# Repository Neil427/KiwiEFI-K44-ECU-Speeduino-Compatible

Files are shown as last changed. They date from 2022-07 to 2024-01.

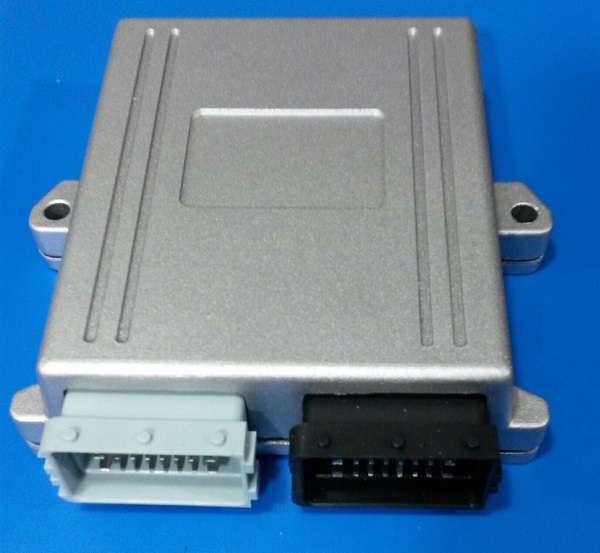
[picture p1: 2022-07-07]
Hardware/KiwiEfi K44 ECU enclosure.png

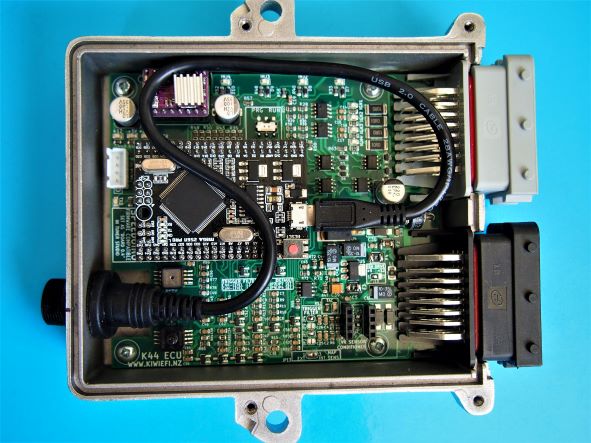
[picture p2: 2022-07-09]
K44_ECU_Inside.JPG

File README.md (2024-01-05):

# Speeduino-KiwiEFI-K44-ECU
The KiwiEFI K44 ECU is designed to run Speeduino firmware and is designed to be 100% compatible with the Speeduino V0.4 Mega2560 pin specification. 
In Tuner Studio select ecu type as V0.4.
  Features:
- 4 layer pcb for good noise immunity, reliable operation.
- 2x 24pin sealed automotive connectors.
- See specifications file for full details.



Open source design for those wishing to build from scratch.

Or will be available for purchase at www.kiwiefi.nz fully built up with mating loom connectors, (firmware/base tune loaded and tested on a real engine) . 

If you would like to save some freight costs and purchase just the pcb fitted with all smd components only (i.e. less box, connectors, arduino, and all other throughhole components) please contact me through www.kiwiefi.nz

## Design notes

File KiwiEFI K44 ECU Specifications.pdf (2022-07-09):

## KiwiEFI K44 Specifications

- 48-pin connector and splash proof case
- 4 injector channels with internal diagnostic LEDs
- 4 Ignition outputs with internal diagnostic LEDs
- CLT, IAT, TPS and O2 inputs
- Inbuilt Hall Effect Sensor blocking diodes and pullups for crank and Cam inputs
- Socket for VR conditioner module(crank and cam input conditioning)
- Inbuilt Baro sensor
- External MAP sensor and internal Map sensor option.
- Socket for DRV8825 stepper module (stepper idle valve control)
- 8 medium-current spare outputs for Fuel pump relay, Fan relay, Boost control, VVT1, VVT2, Idle1, Idle2, Tach + the 4 stepper module outputs.
- Clutch switch digital input.
- Flex fuel digital input.
- 2 spare unassigned digital inputs.
- 2 spare unassigned analog inputs.
- 1 spare unassigned connector pin for custom use.
- Speeduino v0.4 board compatible pin definition, select as board type V0.4 in Tuner Studio
- 2x Serial output, TTL level (Ser0) for Bluetooth on internal connector and RS232 level driver on Secondary Serial (Ser3) TXD and RXD on ecu connector for sending data to dashes etc.
- Uses the same case as the Speeduino Dropbear ECU and is mostly pin compatible with the Dropbear., (the only pinout differences are 1: IG5-IG8 pins are used for digital outputs, as there are only 4 ignition outputs, 2: INJ5-INJ8 pins are fed in parallel with INJ1-INJ4 for paired injectors on a 6/8 cyl, and 3: the CAN bus pins are used for Serial3 RS232 data )

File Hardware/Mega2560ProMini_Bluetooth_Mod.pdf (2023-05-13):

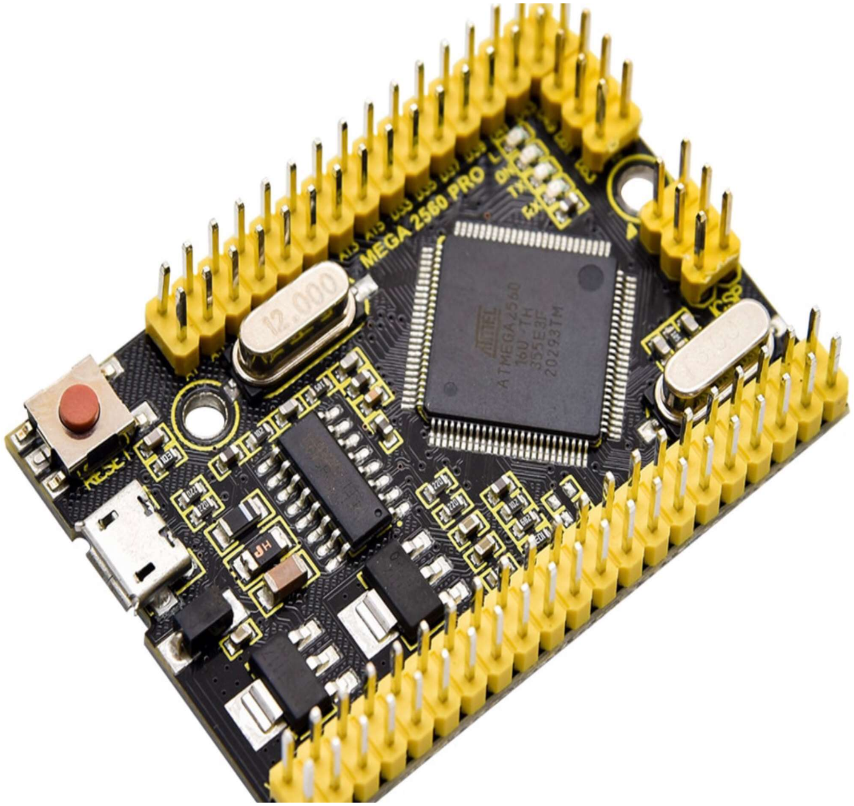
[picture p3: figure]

# MEGA2560 PRO MINI

## Speeduino Serial 0 HC-06 Bluetooth Mod

Note: no guarantee this works with all Pro Mini / HC-06, but works with all I have tried.

The use of blue-tooth connection to Tuner Studio as described in the Speeduino Wiki works on a full sized MEGA2560 board but not on the Pro Mini version. This is due to the value of the resistors used to connect the USB-Serial chip to the TX0/RX0 pins on the MCU chip and header pins.

The full sized Mega2560 that use the 16U2 for USB-Serial conversion have 1K resistors, thus when you attach the blue-tooth module, as in the Speeduino Wiki, it connects to the header pins and thus directly to the MCU pins. The 16U2 chip is still attached to the MEGA TX0/RX0 pins through 1K resistors, the load produced by this can be overcome by the blue-tooth module so it all works.

However the PRO MINI uses a CH340G usb-serial chip connected to the MCU and TX0/RX0 pins through 22R resistors, this low resistance loads the blue-toothTX / Mega RX signal too much stopping the blue-tooth working.

The picture below shows the resistors, one goes to the ProMini TX0 pin and one to the RX0 pin.

The fix I have found to work is to change the 22R (marked as 220 in SMD marking format) that is attached to the ProMini RX0 pin to 220R (either 221 or 2200 in SMD marking format). This reduces the loading on the bluetooth module enough to make it work. You should use a multi-meter to identify which of the two resistors to change as I have found some ProMinis with small layout differences that swap the PCB position of the TX and RX resistors.

(Swapping both resistors does seem to work but it will degrade the low level logic level of the Mega2560 TX0 signal due to the voltage divider produced with the TX LED dropping resistor.)

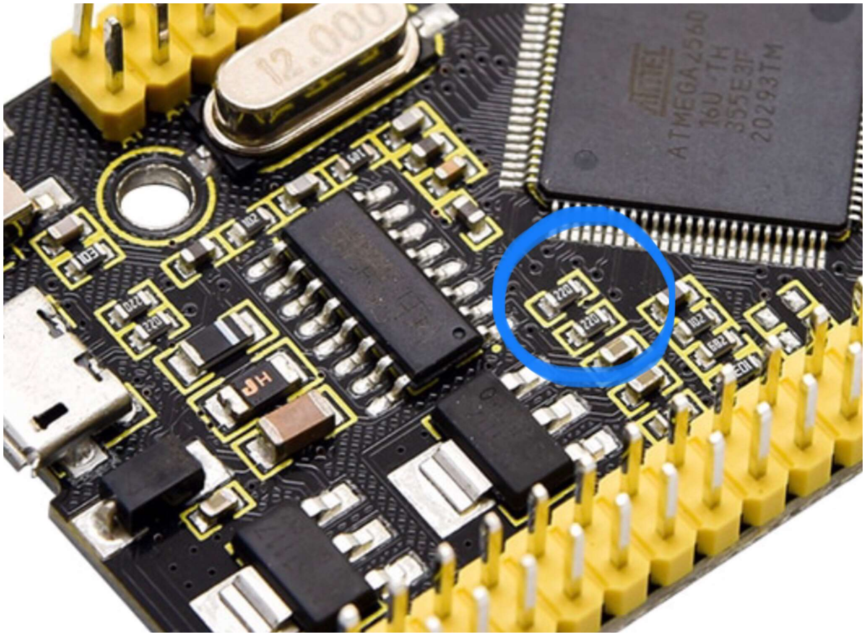
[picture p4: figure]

If you never wish to use Bluetooth you should leave the resistors as 22R as it gives better logic voltage levels between the CH340 and Atmega2560.

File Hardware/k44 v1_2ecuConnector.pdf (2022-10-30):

Sheet1

Page 1

## K44 48-PIN ECU CONNECTOR PINOUT

GREY CONNECTOR | BLACK CONNECTOR
C1 | C2 | C3 | C4 | C5 | C6 | C7 | C8 | C1 | C2 | C3 | C4 | C5 | C6 | C7 | C8
BOOST | FAN | STEP-B2 | STEP-B1 | STEP-A1 | STEP-A2 | FP | GND | GND | AN IN1 | AN IN2 | OXY | CTS | IAT | TPS | MAP
HC4 | LC2 | | | | | LC1 | | SENSOR
B1 | B2 | B3 | B4 | B5 | B6 | B7 | B8 | B1 | B2 | B3 | B4 | B5 | B6 | B7 | B8
IGN1 | IGN2 | IGN3 | IGN4 | IDL2 | IDL1 | VVT1 | VVT2 | TAC | CNK+ | CNK- | CAM+ | CAM- | DIG IN1 | LAUNCH | FLEX
| | | | HC1 | HC3 | HC2 | HC5 | | TRIG1 | TRIG1 | TRIG2 | TRIG2
A1 | A2 | A3 | A4 | A5 | A6 | A7 | A8 | A1 | A2 | A3 | A4 | A5 | A6 | A7 | A8
INJ1 | INJ2 | INJ3 | INJ4 | INJ5 | INJ6 | INJ7 | INJ8 | +12V | GND | +5V OUT | O/P | DIG IN2 | RXD | TXD | GND
| | | | | | | | POWER | POWER | | PIN43 | | SERIAL3 | SERIAL3 | DIGITAL

NOTE: VIEW LOOKING INTO ECU BOX CONNECTORS. (PIN NUMBERS ARE MOLDED INTO REAR OF LOOM CONNECTOR)
A1 | OUTPUT | INJECTOR 1 | A1 | POWER | +12V POWER INPUT From ignition relay
A2 | OUTPUT | INJECTOR 2 | A2 | POWER GROUND | (ground at engine block with its own 1mm wire)
A3 | OUTPUT | INJECTOR 3 | A3 | POWER
A4 | OUTPUT | INJECTOR 4 | A4 | OUTPUT | SPARE OUTPUT DEFAULT SET TO MCU PIN 43
A5 | OUTPUT | INJECTOR 5 | A5 | INPUT | DIGITAL INPUT 2
A6 | OUTPUT | INJECTOR 6 | A6 | COMMS | SERIAL3 DATA RXD
A7 | OUTPUT | INJECTOR 7 | A7 | COMMS | SERIAL3 DATA TXD
A8 | OUTPUT | INJECTOR 8 | A8 | DIGITAL I/P GROUND | GROUND FOR DIGITAL INPUTS AND SERIAL DATA
B1 | OUTPUT | IGNITION 1 | B1 | OUTPUT | TACH OUTPUT Pulled up to +12v
B2 | OUTPUT | IGNITION 2 | B2 | TRIGGER
B3 | OUTPUT | IGNITION 3 | B3 | TRIGGER
B4 | OUTPUT | IGNITION 4 | B4 | TRIGGER
B5 | OUTPUT | IDL2 when configured for 3-wire idle valve | B5 | TRIGGER
B6 | OUTPUT | B6 | INPUT | DIGITAL INPUT 1
B7 | OUTPUT | B7 | INPUT | CLUTCH SWITCH INPUT
B8 | OUTPUT | VVT2 when configured for dual VVT | B8 | INPUT | FLEX FUEL SENSOR INPUT
C1 | OUTPUT | C1 | SENSOR GND
C2 | OUTPUT | C2 | INPUT | ANALOG INPUT 1
C3 | OUTPUT | IDLE STEPPER B2 OUTPUT | C3 | INPUT | ANALOG INPUT 2
C4 | OUTPUT | IDLE STEPPER B1 OUTPUT | C4 | INPUT | OXY SENSOR INPUT 0-5V
C5 | OUTPUT | IDLE STEPPER A1 OUTPUT | C5 | INPUT | COOLANT TEMPERATURE SENSOR
C6 | OUTPUT | IDLE STEPPER A2 OUTPUT | C6 | INPUT | INTAKE AIR TEMPERATURE SENSOR
C7 | OUTPUT | C7 | INPUT | THROTTLE POSITION SENSOR
C8 | POWER GROUND (Ground at engine block with its own 1mm wire) | C8 | INPUT | EXTERNAL MAP SENSOR INPUT (internal Map switch set to EXT.)

+5V SENSOR POWER (MAXCURRENT 100mA)

CRANK SENSOR +ve
CRANK SENSOR -ve (only for VR, for Hall use pin A8) CAM SENSOR +ve
CAM SENSOR -ve (only for VR, for Hall use pin A8) IDL1 SOLENOID gnd active drive VVT1 SOLENOID gnd active drive

BOOST SOLENOID gnd active drive FAN RELAY gnd active drive

FUEL PUMP Gnd active Relay Drive

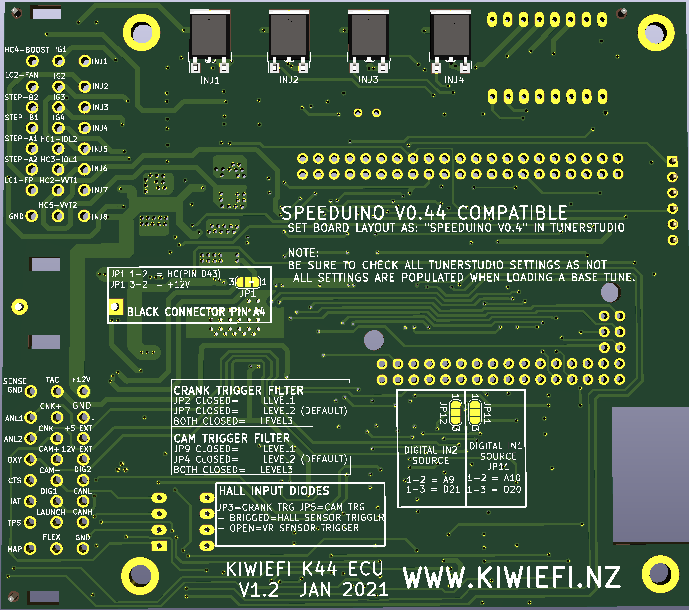
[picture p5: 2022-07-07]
Hardware/PCBbottom.png

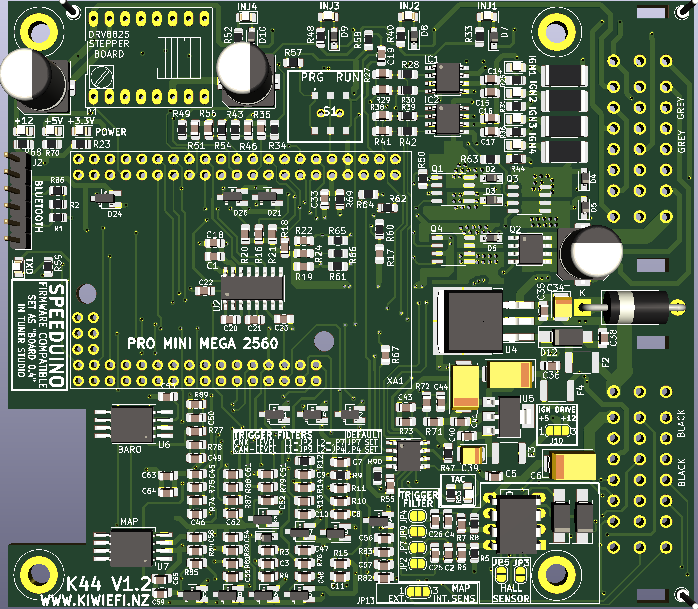
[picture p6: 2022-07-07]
Hardware/PCBtop.png

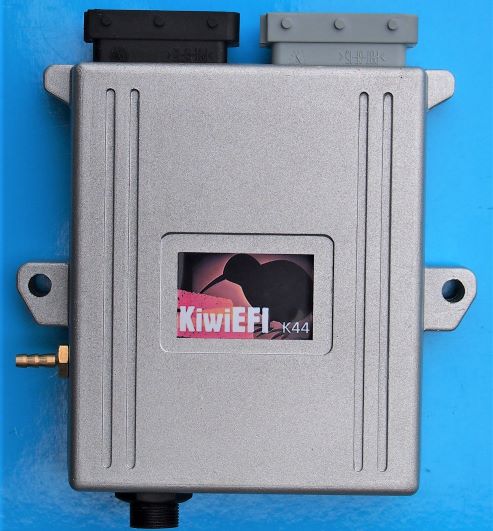
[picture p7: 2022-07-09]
K44_ECU.jpg

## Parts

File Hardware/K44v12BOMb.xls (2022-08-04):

KiwiEFI K44 BOM
Item | Qty | Reference(s) | Value | Footprint
1 | 10 | C1, C15, C17, C20, C21, C22, C23, C33, C63, C65 | 1uF 50V | 0805
2 | 2 | C2, C4 | 10N 50V | 0805
3 | 21 | C3, C5, C7, C9, C14, C16, C18, C35, C36, C38, C40, C41, C43, C45, C47, C51, C53, C54, C58, C61, C64 | 100N 50V | 0805
4 | 3 | C6, C37, C42 | 10uF 25V | Tantalum_Kemet-D
5 | 8 | C8, C10, C11, C44, C48, C52, C55, C59 | 220N 50V | 0805
6 | 2 | C12, C13 | 100uF 35V | Elec_8x10
7 | 1 | C19 | 22uF 50V | 0805
8 | 1 | C24 | 220uF25V | Elec_8x10
9 | 1 | C25 | 4N7 50V | 0805
10 | 1 | C26 | 22N 50V | 0805
11 | 2 | C34, C39 | 47uF 25V | Tantalum_Kemet-B
12 | 4 | C46, C50, C57, C62 | 330N 50V | 0805
13 | 2 | C49, C56 | 47pF 50V | 0805
14 | 1 | D1 | MM3Z5V1ST1G | SOD-323
15 | 9 | D2, D3, D4, D5, D6, D7, D8, D9, D10 | 1N4448WX-TP | SOD-323
16 | 14 | D11, D14, D15, D16, D17, D18, D19, D20, D21, D22, D23, D24, D25, D26 | BAT54S | SOT-23
17 | 1 | D12 | B130-13-F | SMA
18 | 1 | D13 | MR2535L | DO-201AE
19 | 2 | D27, D28 | B130-13-F | SMA
20 | 1 | F2 | 0.5A POLYFUSE | 1812
21 | 2 | F3, F4 | 0.25A POLYFUSE | 1812
22 | 2 | IC1, IC2 | TC4424A | SOIC-8_3.9x4.9mm_P1.27mm
23 | 1 | J1 | Conn_02x24_Male | Delphi_48pinConnectorBox_AandBconnectors
24 | 1 | J2 | BLUETOOTH 1 tx/rx0 | PinHeader_1x06_P2.54mm_Vertical
25 | 3 | J3, J4, J6 | TOOLING HOLE | ToolingHole
26 | 1 | J5 | TRIGGER CONDITIONER | DIP-8_W7.62mm
27 | 12 | LED1, LED2, LED3, LED4, LED5, LED6, LED7, LED8, LED10, LED11, LED12, LED13 | GREEN LED | 0805
28 | 1 | LED9 | BLUE LED | 0805
29 | 1 | P1 | DRV8825 | DRV8825_STEPPER
30 | 3 | Q1, Q3, Q4 | VNS3NV04D | SO-8_3.9x4.9mm_P1.27mm
31 | 2 | Q2, Q7 | NCV8402AD | SOIC-8_3.9x4.9mm_P1.27mm
32 | 4 | Q5, Q6, Q8, Q9 | NCV8408 | ATPAK-2
33 | 3 | R1, R2, R86 | 1K | 0805
34 | 1 | R3 | 1K | 0805
35 | 20 | R4, R11, R14, R16, R17, R18, R19, R20, R21, R22, R24, R27, R29, R35, R38, R41, R46, R51, R55, R56 | 51K | 0805
36 | 13 | R5, R8, R9, R12, R28, R30, R34, R39, R42, R43, R47, R49, R54 | 1K | 0805
37 | 3 | R6, R7, R67 | 220R | 0805
38 | 11 | R10, R13, R72, R74, R76, R77, R79, R81, R82, R85, R87 | 470r | 0805
39 | 1 | R15 | 2K49 | 0805
40 | 1 | R23 | 2K2 | 0805
41 | 9 | R25, R31, R33, R36, R40, R44, R48, R52, R59 | 1K | 0805
42 | 4 | R26, R32, R37, R45 | 10R | 2512
43 | 8 | R50, R60, R61, R62, R63, R64, R65, R66 | 220R | 0805
44 | 2 | R53, R90 | 10K | 0805
45 | 1 | R57 | 10k | 0805
46 | 1 | R58 | 120R | 0805
47 | 1 | R68 | 10K | 0805
48 | 1 | R69 | 10K | 0805
49 | 1 | R70 | 3K9 | 0805
50 | 1 | R71 | 3k9 | 0805
51 | 1 | R73 | 1k | 0805
52 | 4 | R75, R78, R83, R88 | 51k | 0805
53 | 2 | R80, R84 | 2k49 | 0805
54 | 1 | R89 | 1M | 0805
55 | 1 | S1 | SWITCH | AYZ0202AGRLC
56 | 1 | U2 | MAX232 | SOIC-16_3.9x9.9mm_P1.27mm
57 | 1 | U4 | LM2940S-5.0/NOPB | TO-263-3_TabPin2
58 | 1 | U5 | LM2940IMP-5.0/NOPB | SOT-223-3_TabPin2
59 | 1 | U6 | MPXHZ6115A | SSO-8_6.8x5.9mm_P1.27mm
60 | 1 | U7 | MPXHZ6400A | SSO-8_6.8x5.9mm_P1.27mm
61 | 1 | XA1 | Arduino_Mega_Mini | ROBOTDYN Mega2560 PRO MINI 5V (Embed) CH340G

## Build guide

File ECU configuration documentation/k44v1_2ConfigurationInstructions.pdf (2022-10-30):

KiwiEFI K44 ECU CONFIGURATION INSTRUCTIONS V1.2

The K44 is a Speeduino 0.4 compatible ECU using the Mega2560, it uses the Speeduino open source firmware and being 100% compatible with the official hardware version 0.4 it will be able to use all future firmware upgrades written for the 0.4 board.

For documentation and installation instructions for Speeduino ECUs in general please visit wiki.speeduino.com. The following is configuration information specific to the KiwiEFI V44 version of the official Speeduino 0.4 design.
Support and help for Speeduino firmware/hardware can be found at forum.speeduino.com, support and help for the specific KiwiEFI hardware can be obtained via email through our website at KiwiEfi.nz.

## KiwiEFI K44 Specifications

- 48-pin connector and splash proof case
- 4 injector channels with internal diagnostic LEDs
- 4 Ignition outputs with internal diagnostic LEDs
- CLT, IAT, TPS and O2 inputs
- Inbuilt Hall Effect Sensor blocking diodes and pullups for crank and Cam inputs
- Socket for VR conditioner module(crank and cam input conditioning)
- Inbuilt Baro sensor
- External MAP sensor as standard with internal Map sensor available as a optional extra.
- Socket for DRV8825 stepper module (stepper idle valve control)
- 8 medium-current spare outputs for Fuel pump relay, Fan relay, Boost control, VVT1, VVT2, Idle1, Idle2, Tach + the 4 stepper module outputs.
- Clutch switch digital input.
- Flex fuel digital input.
- 2 spare unassigned digital inputs.
- 2 spare unassigned analog inputs.
- Speeduino v0.4 board compatible pin definition, select as board type V0.4 in Tuner Studio
- 2x Serial output, TTL level (Ser0) for Bluetooth on internal connector and RS232 level driver on Secondary Serial (Ser3) TXD and RXD on ecu connector for sending data to dashes etc.
- Uses the same case as the Speeduino Dropbear ECU and is mostly pin compatible with the Dropbear., (the only pinout differences are 1: IG5-IG8 pins are used for digital outputs, as there are only 4 ignition outputs, 2: INJ5-INJ8 pins are fed in parallel with INJ1-INJ4 for paired injectors on a 6/8 cyl, and 3: the CAN bus pins are used for Serial3 RS232 data )

## Board Configuration

The K44 Ecu is compatible with the v0.4 Speeduino configuration, in Tuner Studio setup select board=v0.4.

VR Conditioner – for when using VR crank/cam sensors

Depending on the type of crank and cam sensors you have, there are jumpers that may need to be set. The factory configuration is for Hall effect sensors and Medium signal filtering.

Some VR sensors can send very high AC voltage into the ECU. If you are unsure of your sensor type identify it before connecting it. Using a VR sensor without a VR conditioner may cause damage to the board.

# Jumper Configuration

S1 – PROG-RUN SWITCH
– PROG set to this to update firmware
- RUN set to this for normal operation (default)

J2 – BLUETOOTH CONNECTOR
The Bluetooth connector provides a connection point for a HC-05 Bluetooth module, it is strongly recommended to mount the module or at least its antenna outside the ECU case as the metal case will seriously impact on the range and reliability of the connection.

PIN
1 – HC-05 module (not used) | – connects to MCU D3
2 – HC-05 module pin2 | – connects to VCC
3 – HC-05 module pin3 | – connects to GND
4 – HC-05 module pin4 TXD | – connects to MCU D0 RXD
5 – HC-05 module pin5 RXD | -- connects to MCU D1 TXD
6 – HC-05 module (not used) | -- No Connection

See Speeduino Wiki for Bluetooth configuration details.

Note: the Arduino Mega2560 Pro mini used in this ECU requires 2 resistors to be changed in order to use the Bluetooth option. If your K44 Ecu is purchased as a completed unit from the KiwiEfi.NZ website this modification will have already been done. For details of this modification please contact KiwiEFI.

# Jumpers on Top side of circuit board

Solder jumpers on the top side of the circuit board configure options that may be required to configure the ECU to a specific engine.

JP10 – IGN DRIVE – connect | 1-2 = 5V drive voltage (default) 2-3 = 12V drive voltage
JP13 – MAP SENSOR – connect | 1-2 = External sensor (default) 2-3 = Internal sensor if fitted

We recommend using an external sensor, a wired sensor with short hose to the manifold is faster acting than a long hose to the ECU. An internal sensor of 1bar, 2.5bar, or 4bar is a option available at time of order, or can be fitted later if required.

JP3 & JP5 – HALL SENSOR SELECT
- JOINED = Crank and Cam sensors are Hall effect sensors (default)
- OPEN = Crank and Cam sensors are conditioned by a VR conditioner module NOTE: Make sure these jumpers are OPEN before installing a VR Conditioner module.

CRANK SENSOR FILTER
JP2 joined – TRIGGER FILTER – Crank sensor Level 1 filter
JP7 joined – TRIGGER FILTER – Crank sensor Level 2 filter (default) BOTH JP2 & JP7 joined – Crank sensor Level 3 filter

CAM SENSOR FILTER
JP9 joined – TRIGGER FILTER – Cam sensor Level 1 filter
JP4 joined – TRIGGER FILTER – Cam sensor Level 2 filter (default) BOTH JP9 & JP4 joined – Cam sensor Level 3 filter

## Jumpers on Underside of circuit board

## FACTORY SET - Usually Wont Ever Need To Be Changed

JP11 – DIGIN1 - | 1-2 = connected to function controlled by Arduino pin A10 2-3 = connected to function controlled by Arduino pin D20 (default) (VSS)
JP12 – DIGIN2 - | 1-2 = connected to function controlled by Arduino pin A9 2-3 = connected to function controlled by Arduino pin D21 (default)

JP1 – BLACK ECU PLUG pin A4 – 1-2 = connected to HC o/p controlled by Arduino pin D43
| 2-3 = connected to +12V (for sensors requiring 12V pwr) (default is Connected to D43)

K44 48-PIN ECU CONNECTOR PINOUT

GREY CONNECTOR | BLACK CONNECTOR
C1 | C2 | C3 | C4 | C5 | C6 | C7 | C8 | C1 | C2 | C3 | C4 | C5 | C6 | C7 | C8
BOOST | FAN | STEP-B2 | STEP-B1 | STEP-A1 | STEP-A2 | FP | GND | GND | AN IN1 | AN IN2 | OXY | CTS | IAT | TPS | MAP
HC4 | LC2 | | | | | LC1 | | SENSOR
B1 | B2 | B3 | B4 | B5 | B6 | B7 | B8 | B1 | B2 | B3 | B4 | B5 | B6 | B7 | B8
IGN1 | IGN2 | IGN3 | IGN4 | IDL2 | IDL1 | VVT1 | VVT2 | TAC | CNK+ | CNK- | CAM+ | CAM- | DIG IN1 | LAUNCH | FLEX
| | | | HC1 | HC3 | HC2 | HC5 | | TRIG1 | TRIG1 | TRIG2 | TRIG2
A1 | A2 | A3 | A4 | A5 | A6 | A7 | A8 | A1 | A2 | A3 | A4 | A5 | A6 | A7 | A8
INJ1 | INJ2 | INJ3 | INJ4 | INJ5 | INJ6 | INJ7 | INJ8 | +12V | GND | +5V OUT | O/P | DIG IN2 | RXD | TXD | GND
| | | | | | | | POWER | POWER | | PIN43 | | SERIAL3 | SERIAL3 | DIGITAL

NOTE: VIEW LOOKING INTO ECU BOX CONNECTORS. (PIN NUMBERS ARE MOLDED INTO REAR OF LOOM CONNECTOR)
A1 | OUTPUT | INJECTOR 1 | A1 | POWER | +12V POWER INPUT From ignition relay
A2 | OUTPUT | INJECTOR 2 | A2 | POWER GROUND | (ground at engine block with its own 1mm wire)
A3 | OUTPUT | INJECTOR 3 | A3 | POWER
A4 | OUTPUT | INJECTOR 4 | A4 | OUTPUT | SPARE OUTPUT DEFAULT SET TO MCU PIN 43
A5 | OUTPUT | INJECTOR 5 | A5 | INPUT | DIGITAL INPUT 2
A6 | OUTPUT | INJECTOR 6 | A6 | COMMS | SERIAL3 DATA RXD
A7 | OUTPUT | INJECTOR 7 | A7 | COMMS | SERIAL3 DATA TXD
A8 | OUTPUT | INJECTOR 8 | A8 | DIGITAL I/P GROUND | GROUND FOR DIGITAL INPUTS AND SERIAL DATA
B1 | OUTPUT | IGNITION 1 | B1 | OUTPUT | TACH OUTPUT Pulled up to +12v
B2 | OUTPUT | IGNITION 2 | B2 | TRIGGER | CRANK SENSOR +ve
B3 | OUTPUT | IGNITION 3 | B3 | TRIGGER | CRANK SENSOR -ve (only for VR, for Hall use pin A8)
B4 | OUTPUT | IGNITION 4 | B4 | TRIGGER | CAM SENSOR +ve
B5 | OUTPUT | IDL2 when configured for 3-wire idle valve | B5 | TRIGGER | CAM SENSOR -ve (only for VR, for Hall use pin A8)
B6 | OUTPUT | IDL1 SOLENOID gnd active drive | B6 | INPUT | DIGITAL INPUT 1
B7 | OUTPUT | VVT1 SOLENOID gnd active drive | B7 | INPUT | CLUTCH SWITCH INPUT
B8 | OUTPUT | VVT2 when configured for dual VVT | B8 | INPUT | FLEX FUEL SENSOR INPUT
C1 | OUTPUT | BOOST SOLENOID gnd active drive | C1 | SENSOR GND
C2 | OUTPUT | FAN RELAY gnd active drive | C2 | INPUT | ANALOG INPUT 1
C3 | OUTPUT | IDLE STEPPER B2 OUTPUT | C3 | INPUT | ANALOG INPUT 2
C4 | OUTPUT | IDLE STEPPER B1 OUTPUT | C4 | INPUT | OXY SENSOR INPUT 0-5V
C5 | OUTPUT | IDLE STEPPER A1 OUTPUT | C5 | INPUT | COOLANT TEMPERATURE SENSOR
C6 | OUTPUT | IDLE STEPPER A2 OUTPUT | C6 | INPUT | INTAKE AIR TEMPERATURE SENSOR
C7 | OUTPUT | FUEL PUMP Gnd active Relay Drive | C7 | INPUT | THROTTLE POSITION SENSOR
C8 | POWER GROUND (Ground at engine block with its own 1mm wire) | C8 | INPUT | EXTERNAL MAP SENSOR INPUT (internal Map switch set to EXT.)

+5V SENSOR POWER (MAXCURRENT 100mA)

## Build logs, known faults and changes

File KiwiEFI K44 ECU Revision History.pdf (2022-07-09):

KiwiEFI_K44 Version History

V1.0 - Beta1 pcb design to verify schematic and pcb, minor issues found with mounting holes and connector hole positions. Tested on LS1 V8 with no problems.

V1.01 - Beta 2 pcb test version to confirm mechanical changes to the pcb, cutout for USB cable connector added.

V1.1 - First fully built up ecu tested for 12 months on daily driven LS1 V8 with no failures.
- error found with flyback diode connection for digital outputs, corrected with link on back of pcb.

V1.2 – Work on tidying up a few things before first release.
– PCB change to correct the error with flyback diode connection found in V1.1 pcb.
– Heatsink area on digital output drivers increased to align closer to datasheet recomendations.
– Remove the underside jumpers to select the IGN5-8 alternative function for the IDL,IDL2,VVT,VVT2 connector pins. (Originally these jumpers were to make the ecu 100% pinout compatible with the Dropbear ecu that I was Beta testing on the same vehicle).

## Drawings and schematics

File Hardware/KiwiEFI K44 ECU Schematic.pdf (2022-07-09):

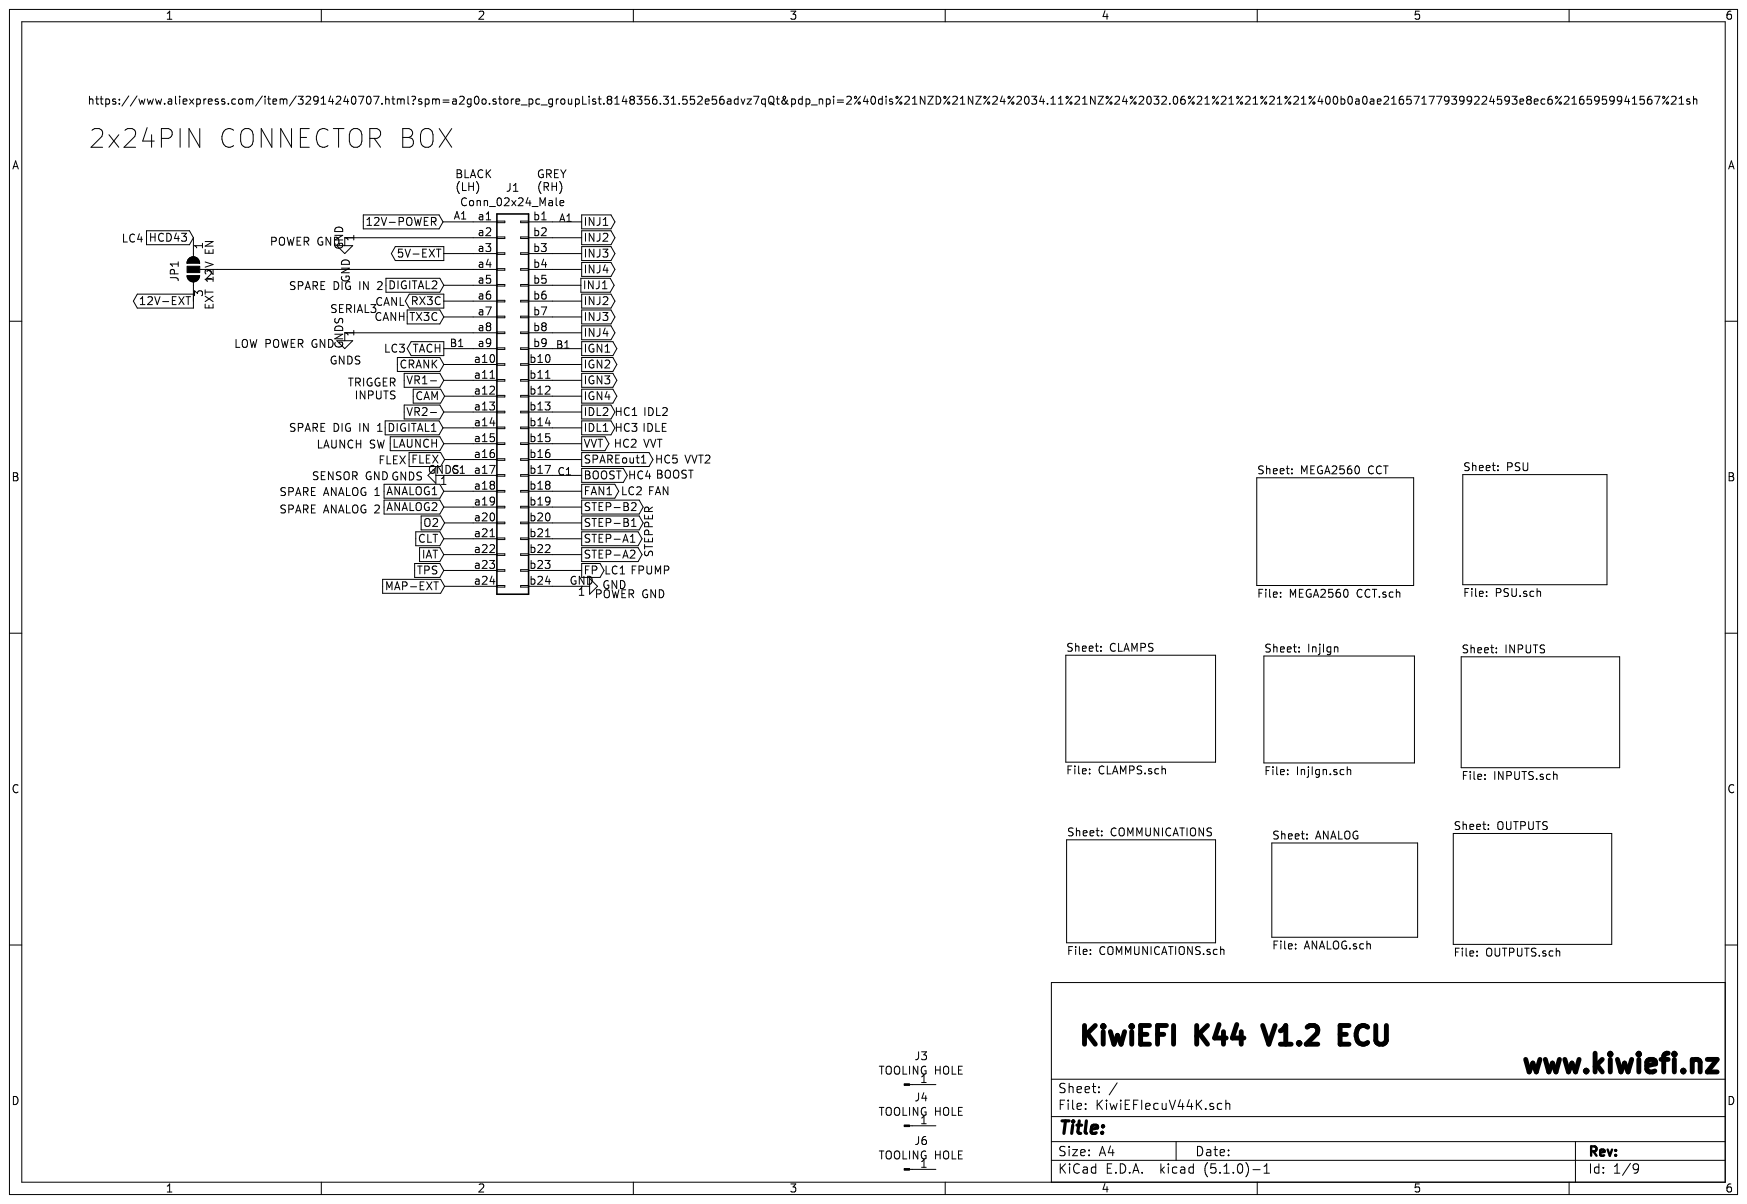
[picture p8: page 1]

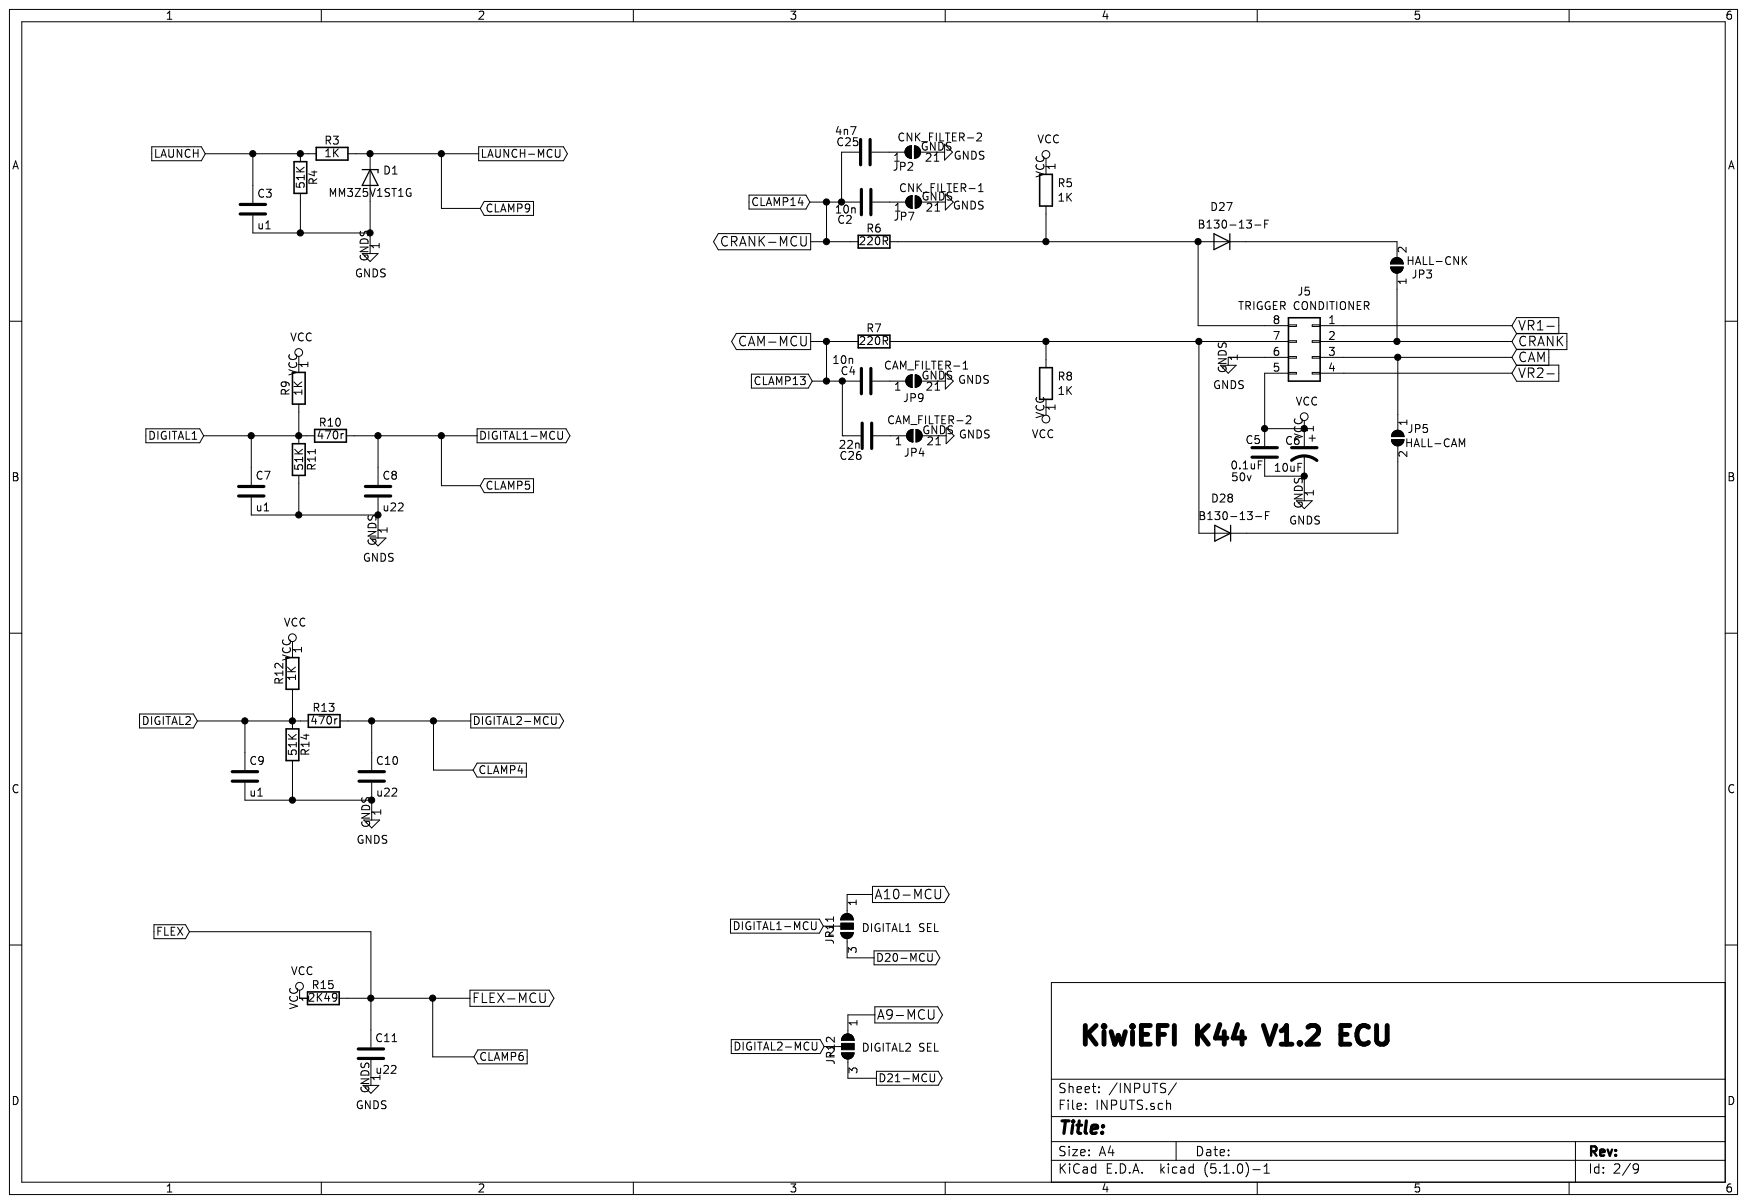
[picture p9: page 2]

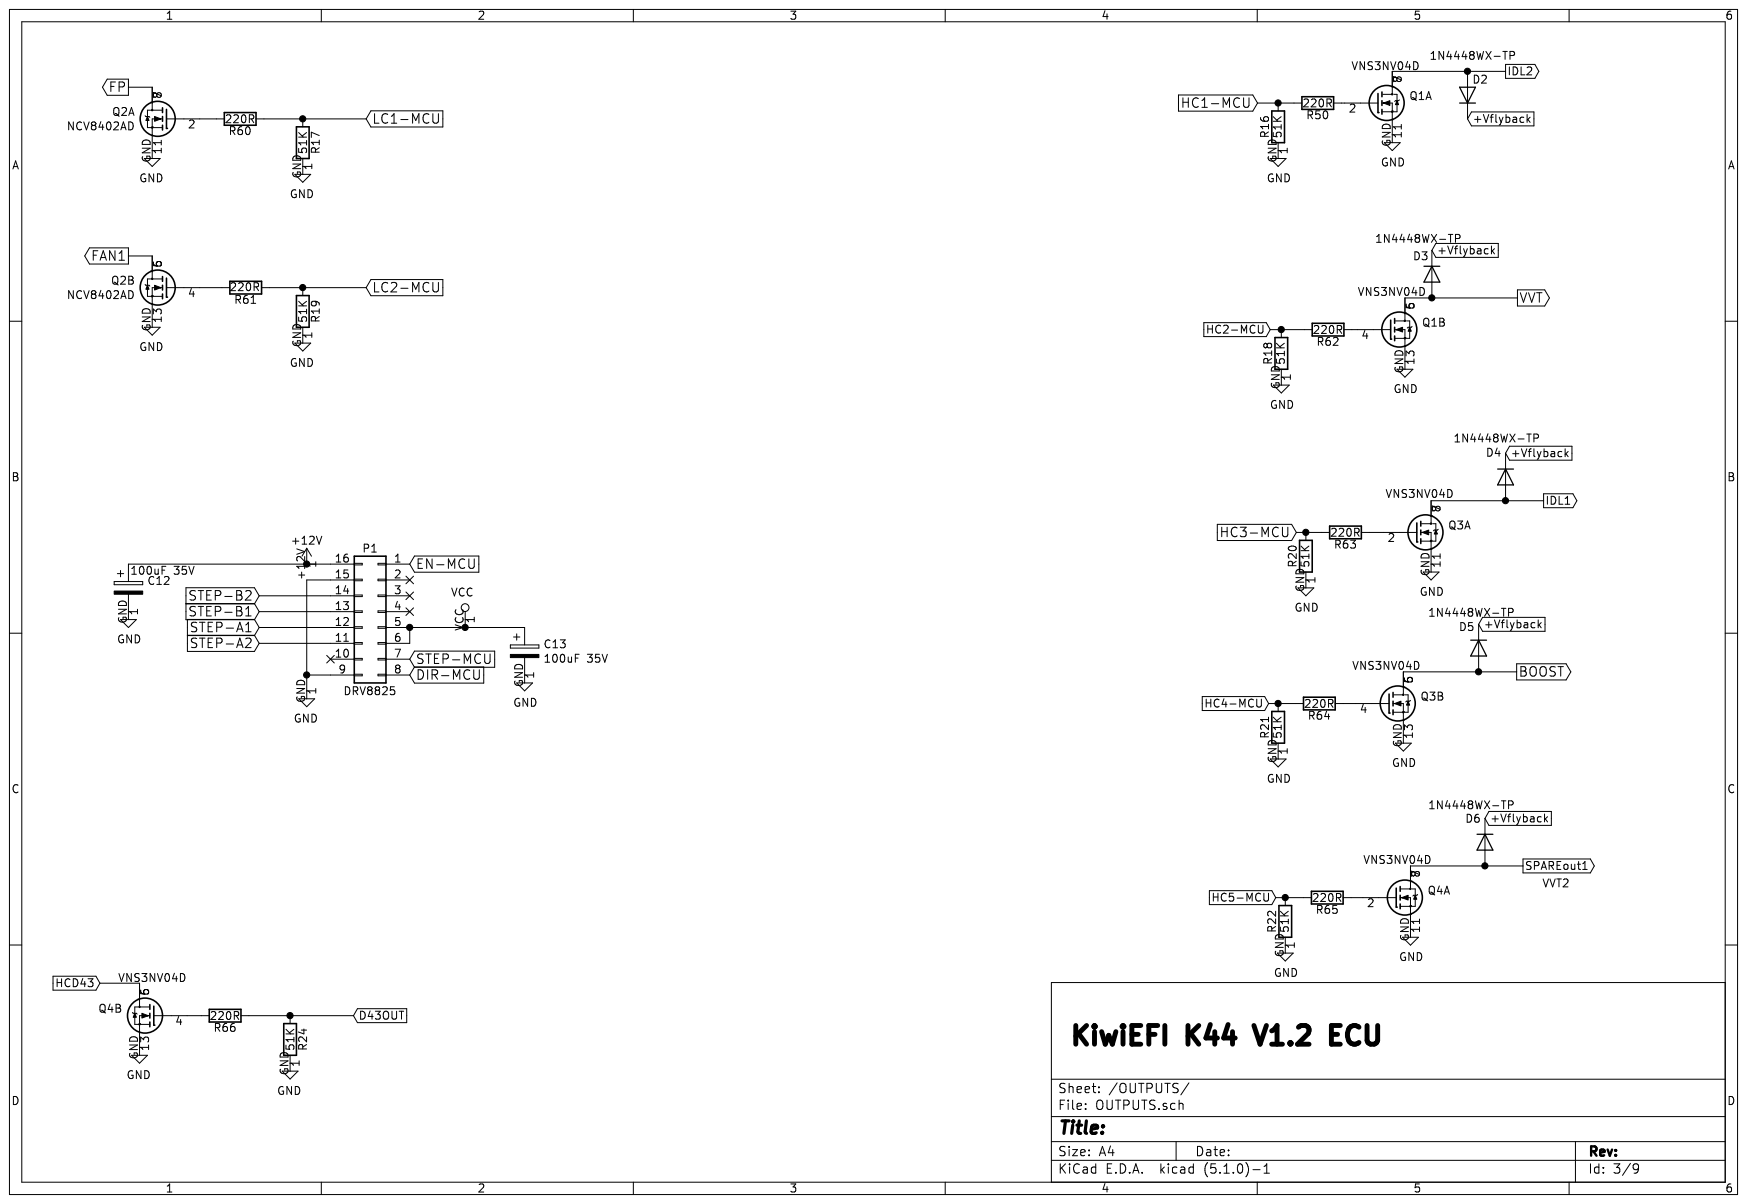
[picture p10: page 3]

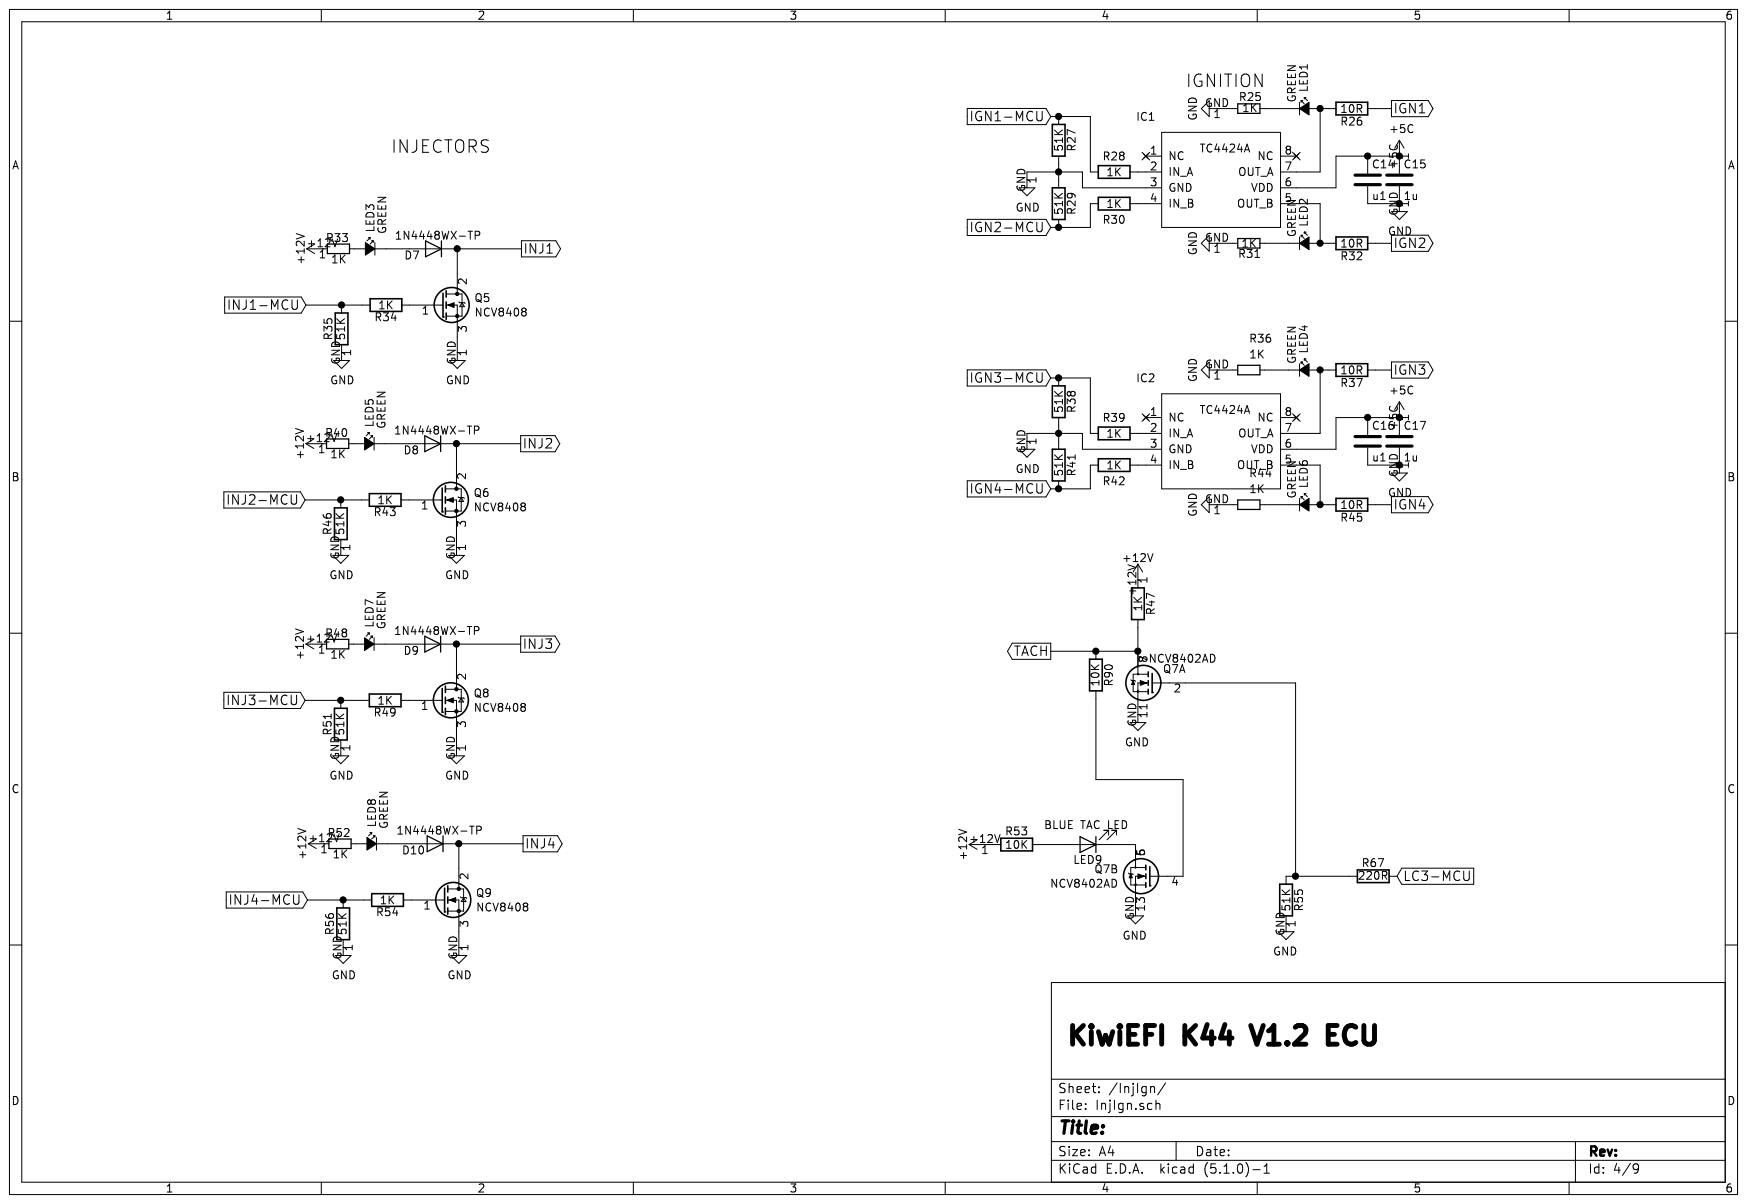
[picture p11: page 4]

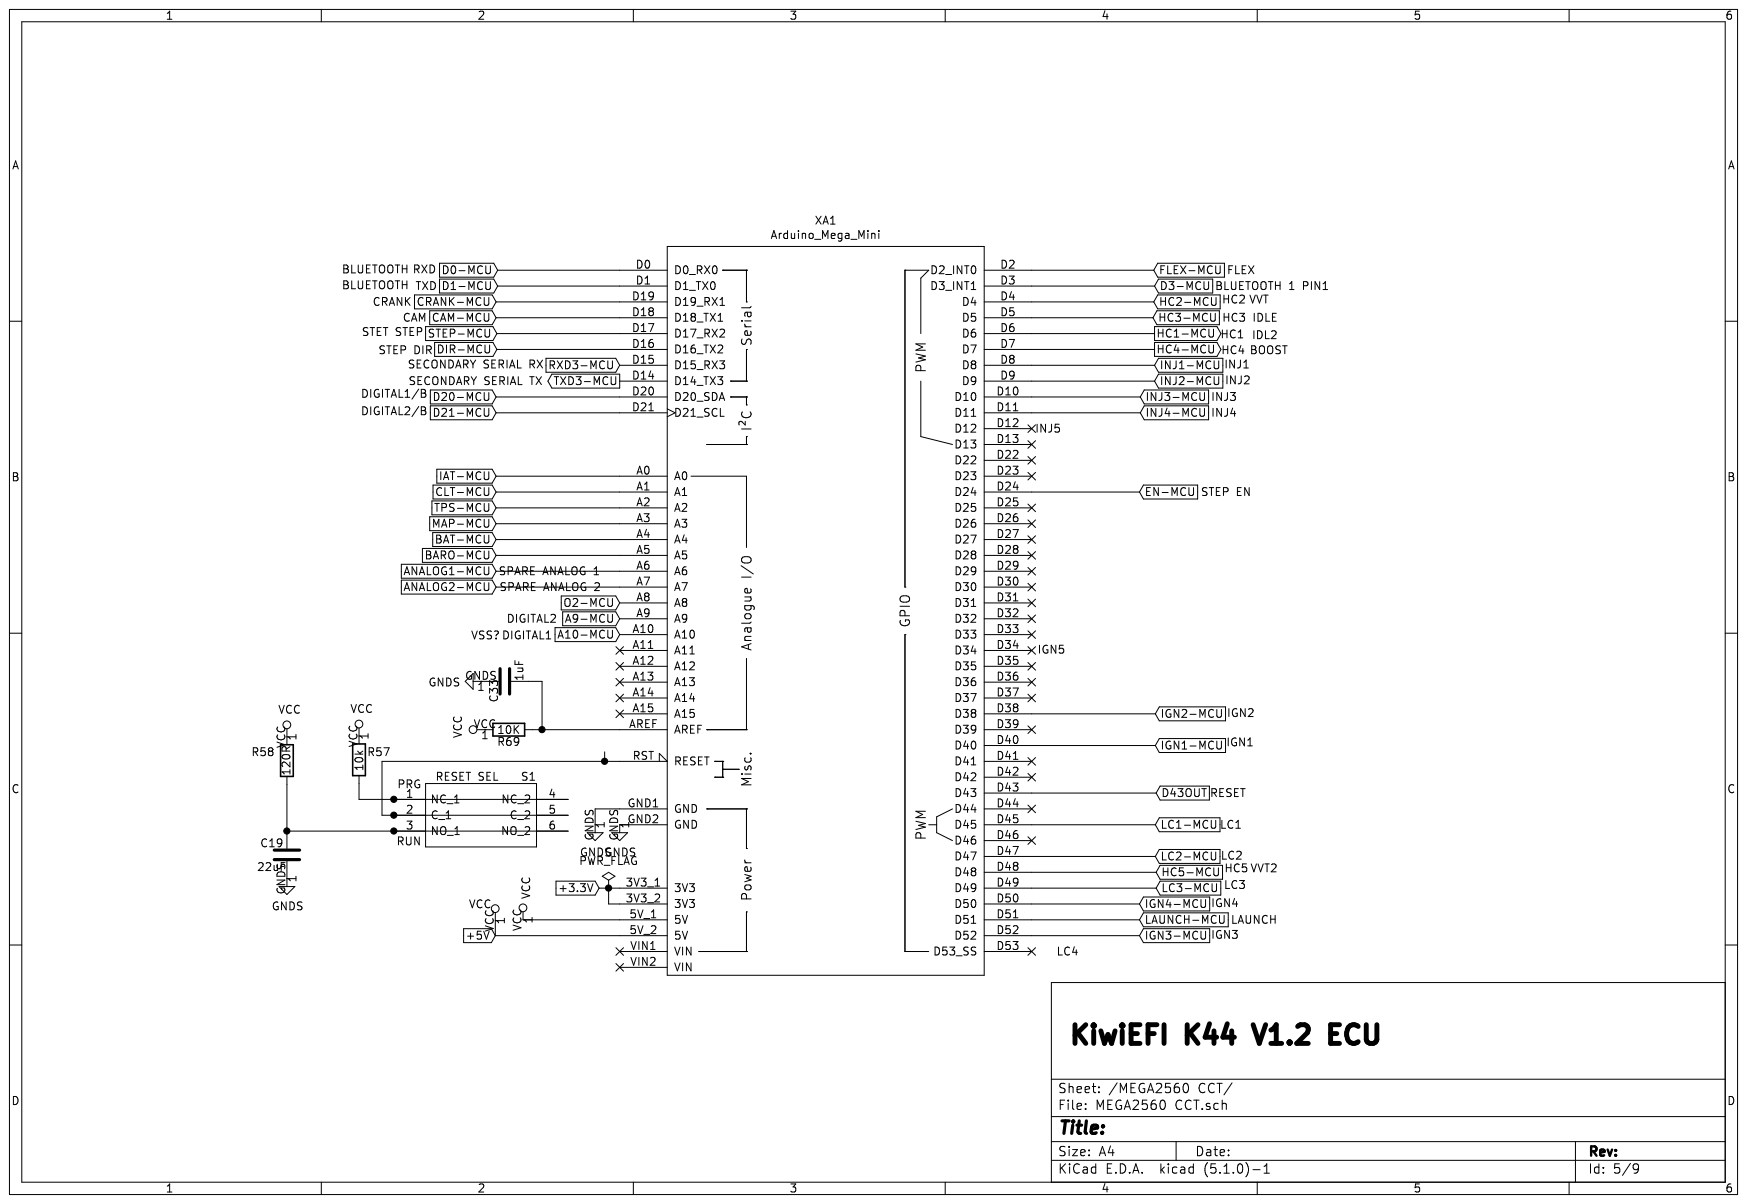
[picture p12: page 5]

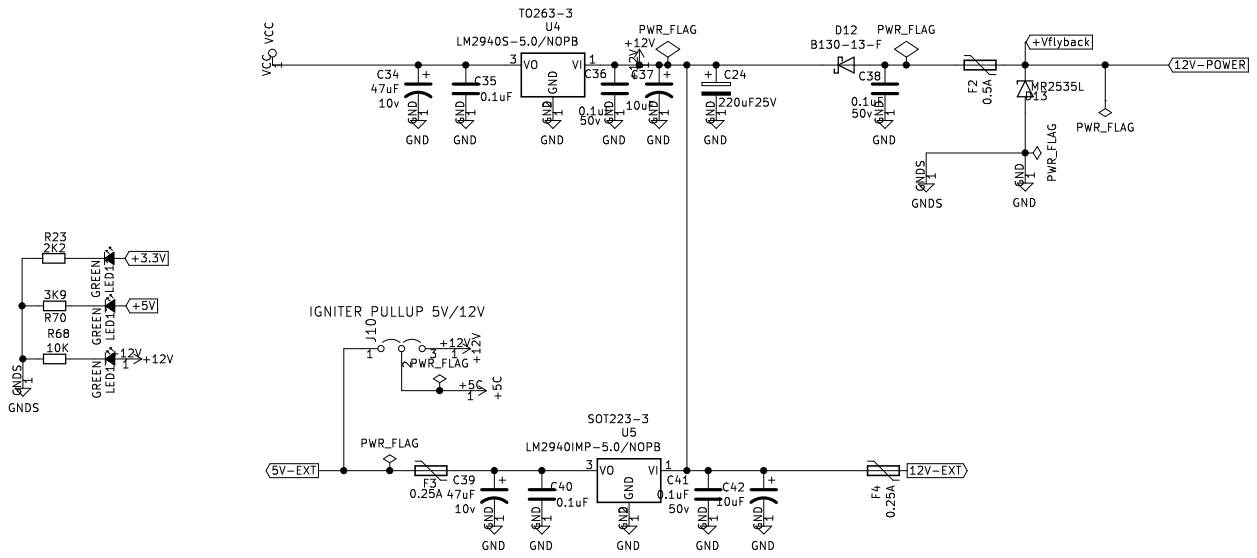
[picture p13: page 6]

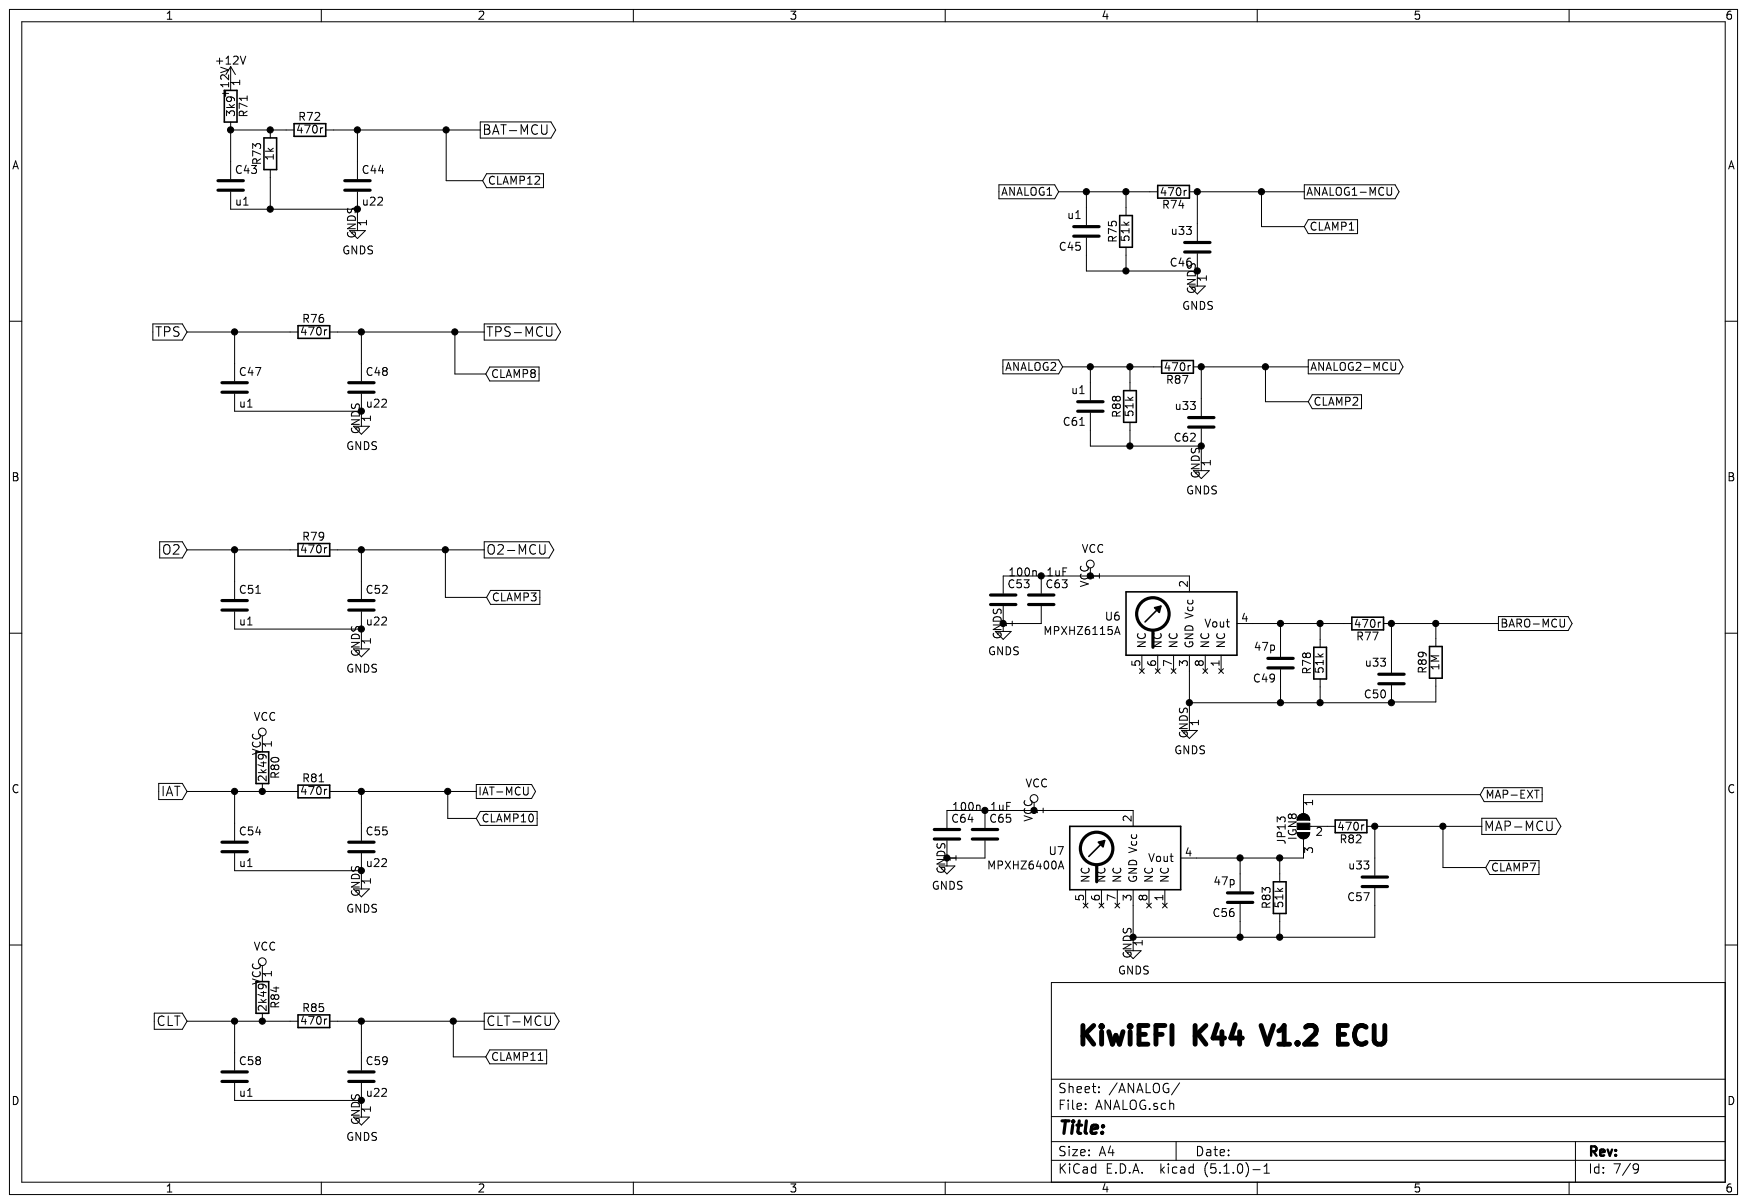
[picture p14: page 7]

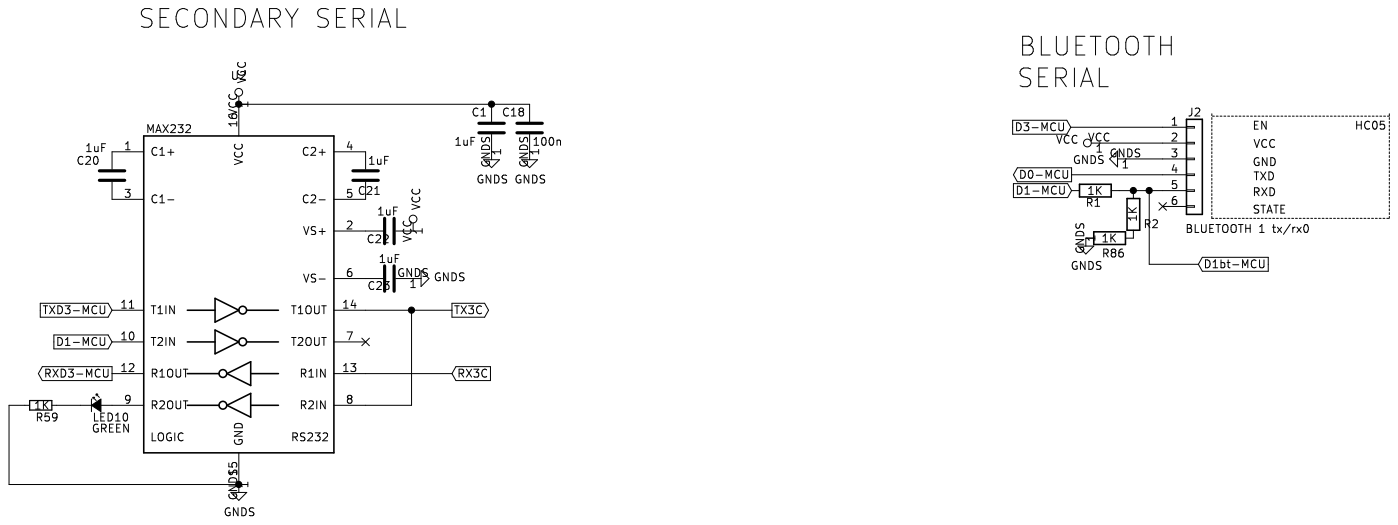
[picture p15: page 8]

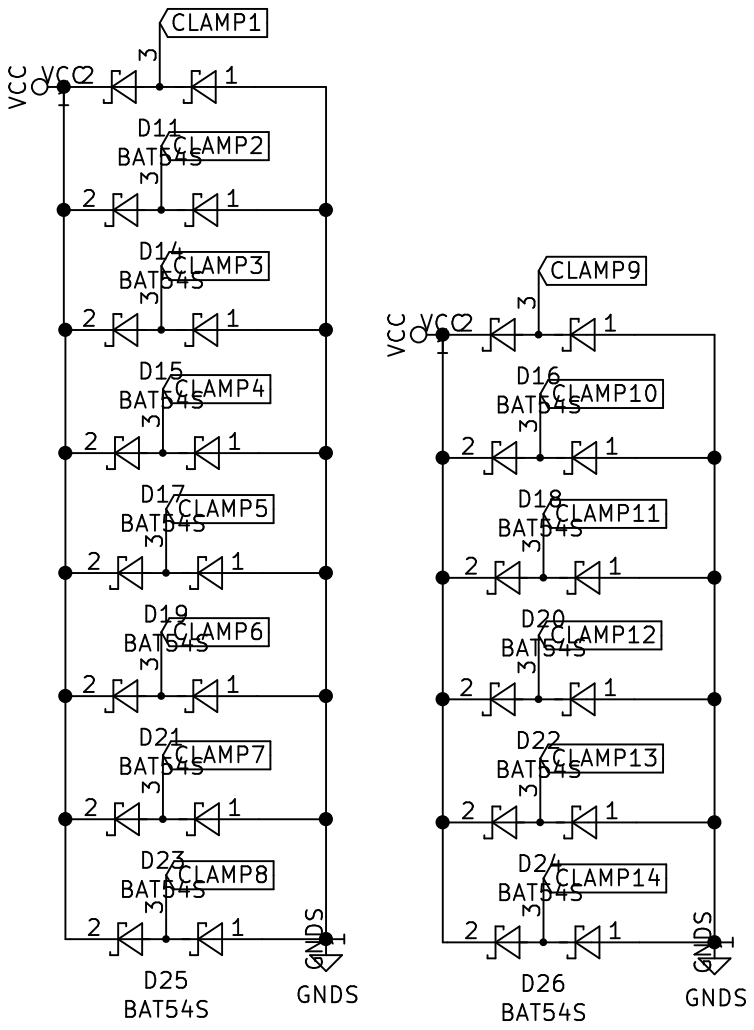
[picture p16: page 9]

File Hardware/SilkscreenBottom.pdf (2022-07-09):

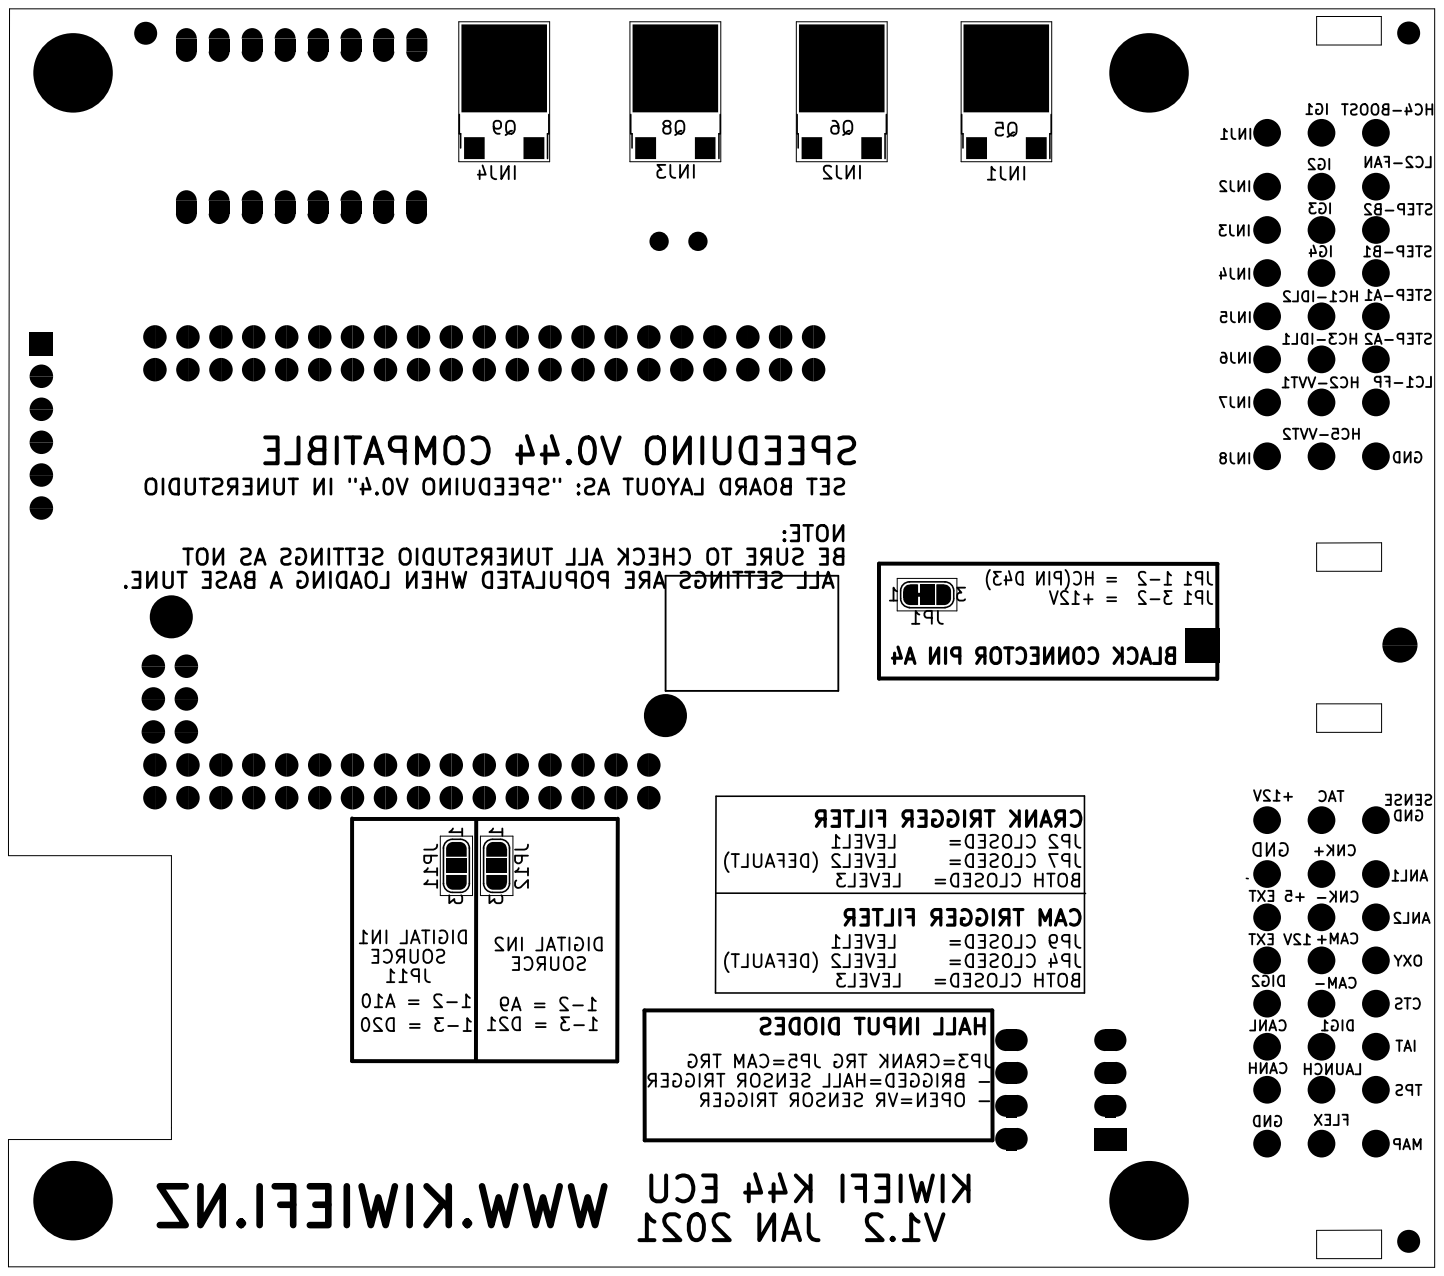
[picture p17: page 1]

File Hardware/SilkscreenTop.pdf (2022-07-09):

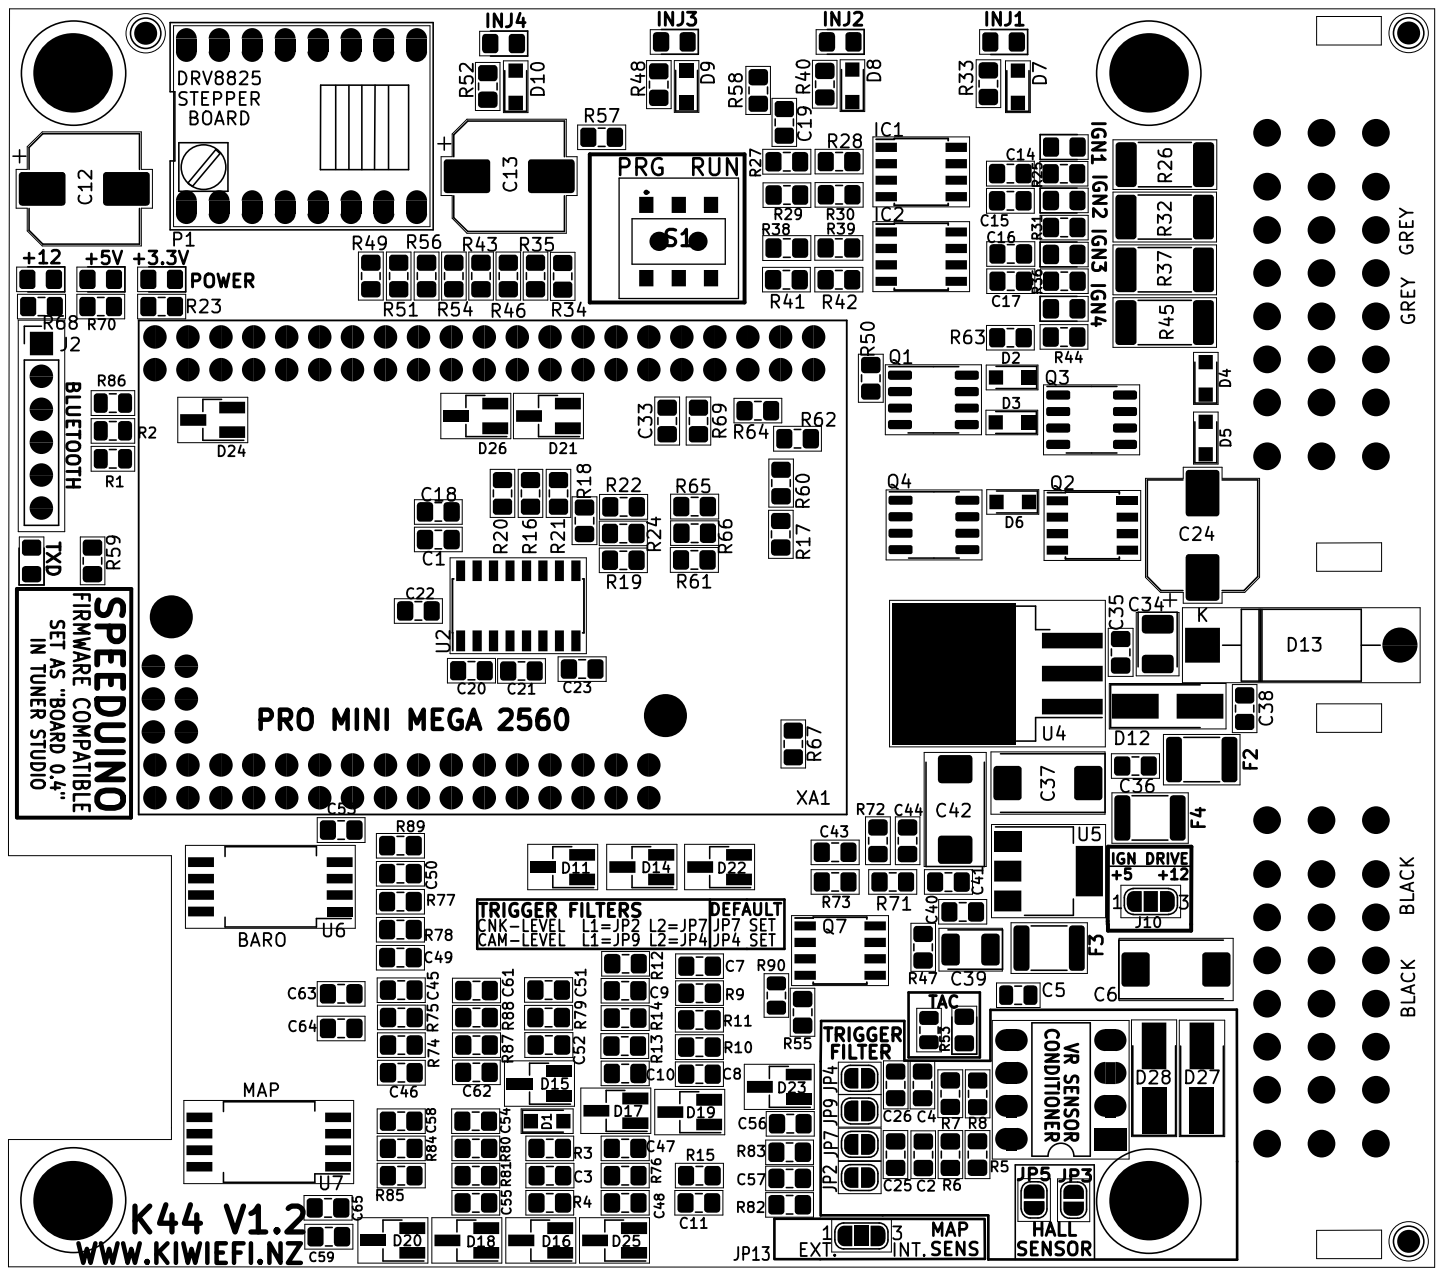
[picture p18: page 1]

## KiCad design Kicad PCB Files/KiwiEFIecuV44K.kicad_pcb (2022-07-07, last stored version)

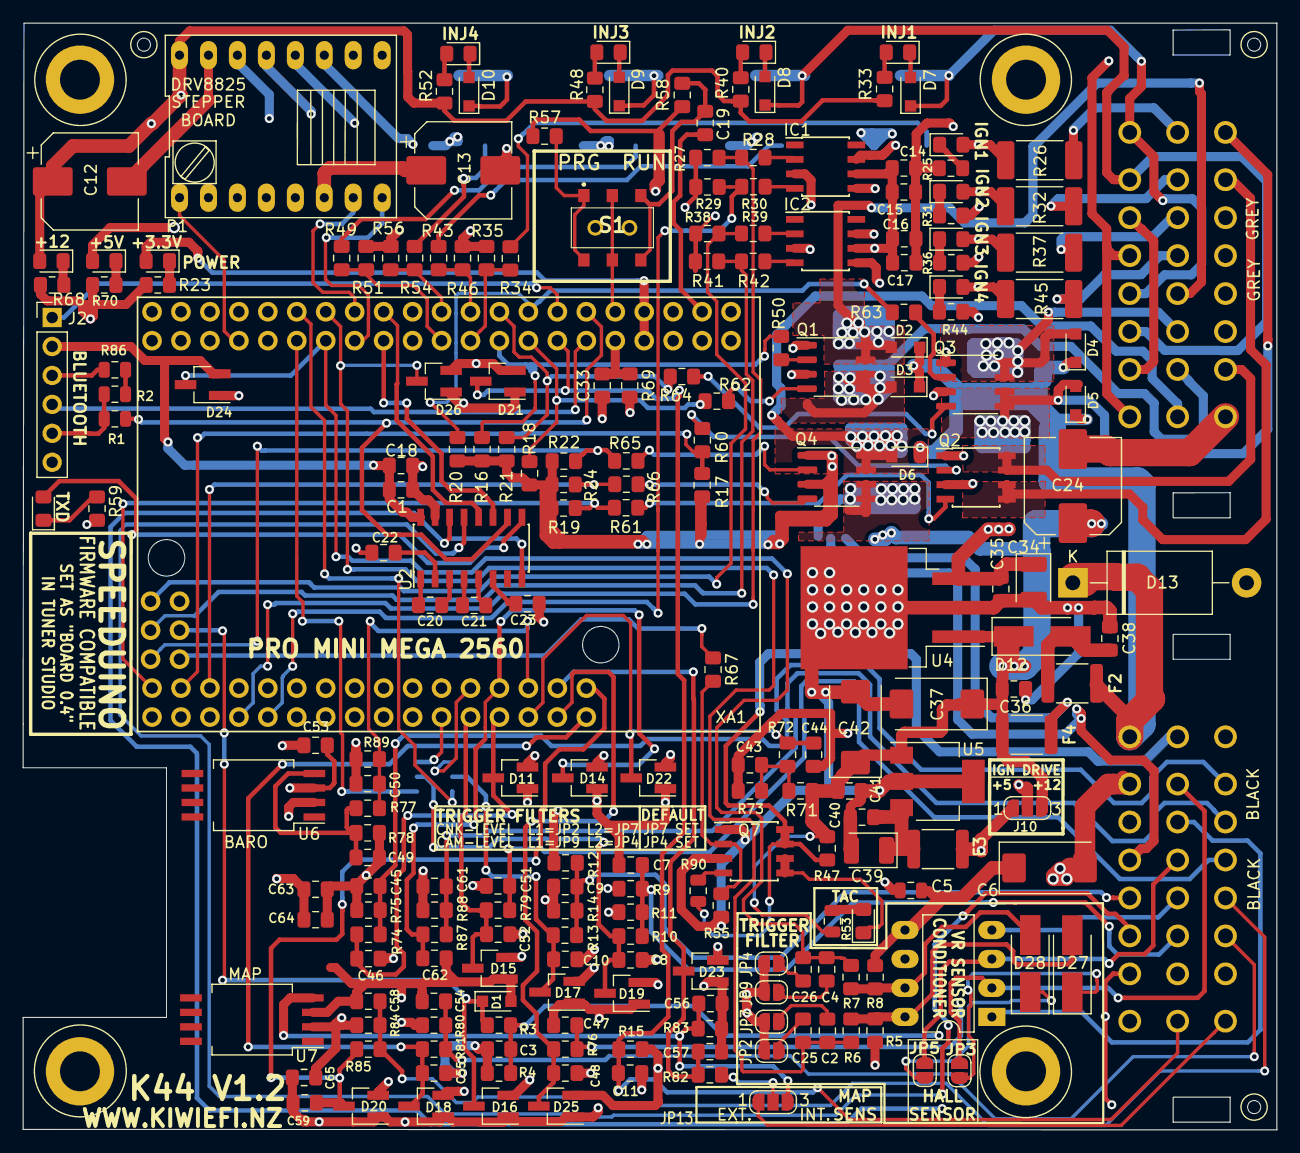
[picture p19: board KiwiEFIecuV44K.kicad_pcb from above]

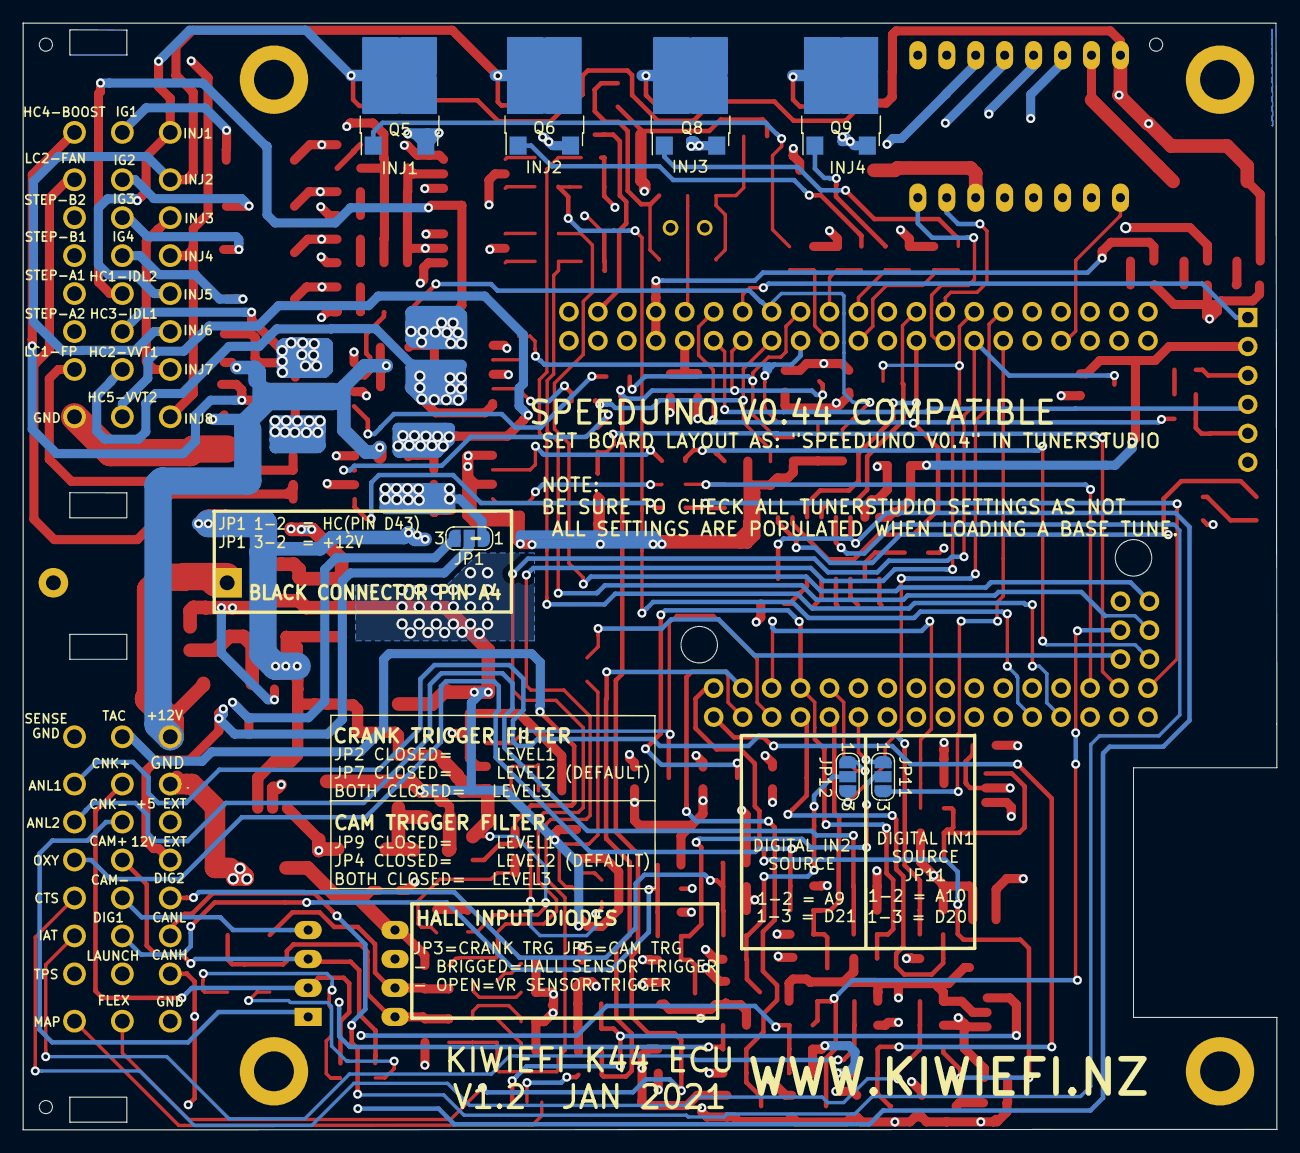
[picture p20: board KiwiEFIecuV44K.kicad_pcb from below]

Board: 4 copper layers, 110.0 x 97.1 mm, 228 parts (7 on the bottom side), 157 nets.

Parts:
C1, C20, C21, C22, C23, C33, C63, C65: 1uF; C_0805_2012Metric_Pad1.15x1.40mm_HandSolder
C2, C4: 10n; C_0805_2012Metric_Pad1.15x1.40mm_HandSolder
C3, C7, C9, C14, C16, C43, C45, C47, C51, C54, C58, C61: u1; C_0805_2012Metric_Pad1.15x1.40mm_HandSolder
C5: 0.1uF; C_0805_2012Metric
C6, C37, C42: 10uF; CP_EIA-7343-31_Kemet-D
C8, C10, C11, C44, C48, C52, C55, C59: u22; C_0805_2012Metric_Pad1.15x1.40mm_HandSolder
C12, C13: 100uF 35V; CP_Elec_8x10
C15, C17: 1u; C_0805_2012Metric_Pad1.15x1.40mm_HandSolder
C18, C53, C64: 100n; C_0805_2012Metric_Pad1.15x1.40mm_HandSolder
C19: 22uF; C_0805_2012Metric_Pad1.15x1.40mm_HandSolder
C24: 220uF25V; CP_Elec_8x10
C25: 4n7; C_0805_2012Metric_Pad1.15x1.40mm_HandSolder
C26: 22n; C_0805_2012Metric_Pad1.15x1.40mm_HandSolder
C34, C39: 47uF; CP_EIA-3528-21_Kemet-B
C35, C36, C38, C40, C41: 0.1uF; C_0805_2012Metric_Pad1.15x1.40mm_HandSolder
C46, C50, C57, C62: u33; C_0805_2012Metric_Pad1.15x1.40mm_HandSolder
C49, C56: 47p; C_0805_2012Metric_Pad1.15x1.40mm_HandSolder
D1: MM3Z5V1ST1G; D_SOD-323_HandSoldering
D2, D3, D4, D5, D6, D7, D8, D9, D10: 1N4448WX-TP; D_SOD-323_HandSoldering
D11, D14, D15, D16, D17, D18, D19, D20, D21, D22, D23, D24, D25, D26: BAT54S; SOT-23_BAT54S
D12, D27, D28: B130-13-F; D_SMA_Handsoldering
D13: MR2535L; D_DO-201AE_P15.24mm_Horizontal
F2: 0.5A; Fuse_1812_4532Metric
F3, F4: 0.25A; Fuse_1812_4532Metric
IC1, IC2: TC4424A; SOIC-8_3.9x4.9mm_P1.27mm
J1: Conn_02x24_Male; Delphi_48pinConnectorBox_AandBconnectors
J2: BLUETOOTH 1 tx/rx0; PinHeader_1x06_P2.54mm_Vertical
J3, J4, J6: TOOLING HOLE; ToolingHole
J5: TRIGGER CONDITIONER; DIP-8_W7.62mm_LongPads
J10: IGNITER PULLUP 5V/12V; SolderJumper-3_P1.3mm_Open_RoundedPad1.0x1.5mm_NumberLabels
JP1: EXT 12V EN; SolderJumper-3_P1.3mm_Open_RoundedPad1.0x1.5mm_NumberLabels
JP2: CNK_FILTER-2; SolderJumper-2_P1.3mm_Open_RoundedPad1.0x1.5mm
JP3: HALL-CNK; SolderJumper-2_P1.3mm_Open_RoundedPad1.0x1.5mm
JP4: CAM_FILTER-2; SolderJumper-2_P1.3mm_Open_RoundedPad1.0x1.5mm
JP5: HALL-CAM; SolderJumper-2_P1.3mm_Open_RoundedPad1.0x1.5mm
JP7: CNK_FILTER-1; SolderJumper-2_P1.3mm_Open_RoundedPad1.0x1.5mm
JP9: CAM_FILTER-1; SolderJumper-2_P1.3mm_Open_RoundedPad1.0x1.5mm
JP11: DIGITAL1 SEL; SolderJumper-3_P1.3mm_Open_RoundedPad1.0x1.5mm_NumberLabels
JP12: DIGITAL2 SEL; SolderJumper-3_P1.3mm_Open_RoundedPad1.0x1.5mm_NumberLabels
JP13: IGN8; SolderJumper-3_P1.3mm_Open_RoundedPad1.0x1.5mm_NumberLabels
LED1, LED2, LED3, LED4, LED5, LED6, LED7, LED8, LED10, LED11, LED12, LED13: GREEN; LED_0805_2012Metric_Pad1.15x1.40mm_HandSolder
LED9: BLUE TAC LED; LED_0805_2012Metric_Pad1.15x1.40mm_HandSolder
P1: DRV8825; DRV8825_STEPPER
Q1, Q3, Q4: VNS3NV04D; SO-8_3.9x4.9mm_P1.27mm
Q2, Q7: NCV8402AD; SOIC-8_3.9x4.9mm_P1.27mm
Q5, Q6, Q8, Q9: NCV8408; ATPAK-2
R1, R2, R86: 1K; R_0805_2012Metric
R3: 1K; C_0805_2012Metric_Pad1.15x1.40mm_HandSolder
R4, R11, R14, R16, R17, R18, R19, R20, R21, R22, R24, R27, R29, R35, R38, R41, R46, R51, R55, R56: 51K; C_0805_2012Metric_Pad1.15x1.40mm_HandSolder
R5, R8, R9, R12, R25, R28, R30, R31, R33, R34, R36, R39, R40, R42, R43, R44, R47, R48, R49, R52, R54, R59: 1K; R_0805_2012Metric_Pad1.15x1.40mm_HandSolder
R6, R7, R67: 220R; C_0805_2012Metric_Pad1.15x1.40mm_HandSolder
R10, R13, R72, R74, R76, R77, R79, R81, R82, R85, R87: 470r; C_0805_2012Metric_Pad1.15x1.40mm_HandSolder
R15: 2K49; C_0805_2012Metric_Pad1.15x1.40mm_HandSolder
R23: 2K2; R_0805_2012Metric_Pad1.15x1.40mm_HandSolder
R26, R32, R37, R45: 10R; R_2512_6332Metric_Pad1.52x3.35mm_HandSolder
R50, R60, R61, R62, R63, R64, R65, R66: 220R; R_0805_2012Metric_Pad1.15x1.40mm_HandSolder
R53, R90: 10K; R_0805_2012Metric
R57: 10k; R_0805_2012Metric_Pad1.15x1.40mm_HandSolder
R58: 120R; R_0805_2012Metric_Pad1.15x1.40mm_HandSolder
R68, R69: 10K; R_0805_2012Metric_Pad1.15x1.40mm_HandSolder
R70: 3K9; R_0805_2012Metric_Pad1.15x1.40mm_HandSolder
R71: 3k9; C_0805_2012Metric_Pad1.15x1.40mm_HandSolder
R73: 1k; C_0805_2012Metric_Pad1.15x1.40mm_HandSolder
R75, R78, R83, R88: 51k; C_0805_2012Metric_Pad1.15x1.40mm_HandSolder
R80, R84: 2k49; C_0805_2012Metric_Pad1.15x1.40mm_HandSolder
R89: 1M; C_0805_2012Metric_Pad1.15x1.40mm_HandSolder
S1: RESET SEL; AYZ0202AGRLC
U2: MAX232; SOIC-16_3.9x9.9mm_P1.27mm
U4: LM2940IMP-5.0/NOPB; TO-263-3_TabPin2
U5: LM2940IMP-5.0/NOPB; SOT-223-3_TabPin2
U6: MPXHZ6115A; SSO-8_6.8x5.9mm_P1.27mm_Clearance8mm
U7: MPXHZ6400A; SSO-8_6.8x5.9mm_P1.27mm_Clearance8mm
XA1: Arduino_Mega_Mini; Arduino_Mega2560_ProMini

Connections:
5V-EXT: F3.2, J1.a3, J10.1
12V-EXT: F4.2, JP1.3
+3.3V: LED11.2, XA1.3V3_1, XA1.3V3_2
+5C: C14.1, C15.1, C16.1, C17.1, IC1.6, IC2.6, J10.2
+5V: C1.1, C5.1, C6.1, C13.1, C18.1, C22.1, C34.1, C35.1, C53.1, C63.1, C64.1, C65.1, D11.2, D14.2, D15.2, D16.2, D17.2, D18.2, D19.2, D20.2, D21.2, D22.2, D23.2, D24.2, D25.2, D26.2, J2.2, J5.5, LED12.2, P1.5, P1.6, R5.1, R8.2, R9.2, R12.2, R15.1, R57.1, R58.2, R69.2, R80.1, R84.1, U2.16, U4.3, U6.2, U7.2, XA1.5V_1, XA1.5V_2
+12V: C12.1, C24.1, C36.1, C37.1, C41.1, C42.1, D12.1, F4.1, J10.3, LED13.2, P1.16, R33.1, R40.1, R47.2, R48.1, R52.1, R53.2, R71.1, U4.1, U5.1
+Vflyback: D2.1, D3.1, D4.1, D5.1, D6.1, D13.1, F2.2, J1.a1
A9-MCU: JP12.1, XA1.A9
A10-MCU: JP11.1, XA1.A10
ANALOG1: C45.2, J1.a18, R74.2, R75.2
ANALOG1-MCU: C46.2, D11.3, R74.1, XA1.A6
ANALOG2: C61.2, J1.a19, R87.2, R88.2
ANALOG2-MCU: C62.2, D14.3, R87.1, XA1.A7
BARO-MCU: C50.2, R77.1, R89.2, XA1.A5
BAT-MCU: C44.1, D22.3, R72.2, XA1.A4
BOOST: D5.2, J1.b17, Q3.5, Q3.6
CAM: J1.a12, J5.3, JP5.1
CAM-MCU: C4.1, C26.2, D24.3, R7.2, XA1.D18
CLAMP3: C52.1, D15.3, R79.2, XA1.A8
CLAMP4: C10.1, D17.3, JP12.2, R13.2
CLAMP5: C8.1, D19.3, JP11.2, R10.2
CLAMP6: C11.1, D21.3, J1.a16, R15.2, XA1.D2
CLAMP7: C57.2, D23.3, R82.1, XA1.A3
CLAMP8: C48.1, D25.3, R76.2, XA1.A2
CLAMP9: D1.1, D16.3, R3.2, XA1.D51
CLAMP10: C55.1, D18.3, R81.2, XA1.A0
CLAMP11: C59.1, D20.3, R85.2, XA1.A1
CLAMP14: C2.2, C25.2, D26.3, R6.2, XA1.D19
CLT: C58.1, J1.a21, R84.2, R85.1
CRANK: J1.a10, J5.2, JP3.1
D0-MCU: J2.4, XA1.D0
D1-MCU: R1.1, U2.10, XA1.D1
D1bt-MCU: J2.5, R1.2, R2.1
D3-MCU: J2.1, XA1.D3
D20-MCU: JP11.3, XA1.D20
D21-MCU: JP12.3, XA1.D21
D43OUT: R24.2, R66.1, XA1.D43
DIGITAL1: C7.1, J1.a14, R9.1, R10.1, R11.1
DIGITAL2: C9.1, J1.a5, R12.1, R13.1, R14.1
DIR-MCU: P1.8, XA1.D16
EN-MCU: P1.1, XA1.D24
FAN1: J1.b18, Q2.5, Q2.6
FP: J1.b23, Q2.7, Q2.8
GND: C1.2, C3.2, C5.2, C6.2, C7.2, C8.2, C9.2, C10.2, C11.2, C12.2, C13.2, C14.2, C15.2, C16.2, C17.2, C18.2, C19.2, C23.1, C24.2, C33.1, C34.2, C35.2, C36.2, C37.2, C38.2, C39.2, C40.2, C41.2, C42.2, C43.2, C44.2, C45.1, C46.1, C47.2, C48.2, C49.1, C50.1, C51.2, C52.2, C53.2, C54.2, C55.2, C56.1, C57.1, C58.2, C59.2, C61.1, C62.1, C63.2, C64.2, C65.2, D1.2, D11.1, D13.2, D14.1, D15.1, D16.1, D17.1, D18.1, D19.1, D20.1, D21.1, D22.1, D23.1, D24.1, D25.1, D26.1, IC1.3, IC2.3, J1.a2, J1.a8, J1.a17, J1.b24, J2.3, J5.6, JP2.2, JP4.2, JP7.2, JP9.2, P1.9, P1.15, Q1.1, Q1.3, Q2.1, Q2.3, Q3.1, Q3.3, Q4.1, Q4.3, Q5.3, Q6.3, Q7.1, Q7.3, Q8.3, Q9.3, R4.2, R11.2, R14.2, R16.1, R17.1, R18.1, R19.1, R20.1, R21.1, R22.1, R23.2, R24.1, R25.2, R27.2, R29.1, R31.2, R35.1, R36.2, R38.2, R41.1, R44.2, R46.1, R51.1, R55.1, R56.1, R59.2, R68.2, R70.2, R73.1, R75.1, R78.1, R83.1, R86.1, R88.1, R89.1, U2.15, U4.2, U5.2, U6.3, U7.3, XA1.GND1, XA1.GND2
HC1-MCU: R16.2, R50.2, XA1.D6
HC2-MCU: R18.2, R62.2, XA1.D4
HC3-MCU: R20.2, R63.2, XA1.D5
HC4-MCU: R21.2, R64.2, XA1.D7
HC5-MCU: R22.2, R65.2, XA1.D48
HCD43: JP1.1, Q4.5, Q4.6
IAT: C54.1, J1.a22, R80.2, R81.1
IDL1: D4.2, J1.b14, Q3.7, Q3.8
IDL2: D2.2, J1.b13, Q1.7, Q1.8
IGN1: J1.b9, R26.1
IGN1-MCU: R27.1, R28.2, XA1.D40
IGN2: J1.b10, R32.1
IGN2-MCU: R29.2, R30.2, XA1.D38
IGN3: J1.b11, R37.1
IGN3-MCU: R38.1, R39.2, XA1.D52
IGN4: J1.b12, R45.1
IGN4-MCU: R41.2, R42.2, XA1.D50
INJ1: D7.1, J1.b1, J1.b5, Q5.2
INJ1-MCU: R34.2, R35.2, XA1.D8
INJ2: D8.1, J1.b2, J1.b6, Q6.2
INJ2-MCU: R43.2, R46.2, XA1.D9
INJ3: D9.1, J1.b3, J1.b7, Q8.2
INJ3-MCU: R49.2, R51.2, XA1.D10
INJ4: D10.1, J1.b4, J1.b8, Q9.2
INJ4-MCU: R54.2, R56.2, XA1.D11
LAUNCH: C3.1, J1.a15, R3.1, R4.1
LC1-MCU: R17.2, R60.1, XA1.D45
LC2-MCU: R19.2, R61.1, XA1.D47
LC3-MCU: R67.1, XA1.D49
MAP-EXT: J1.a24, JP13.1
unnamed: C2.1, JP7.1
unnamed: C4.2, JP9.1
unnamed: C19.1, R58.1, S1.3, S1.6
unnamed: C20.1, U2.1
unnamed: C20.2, U2.3
unnamed: C21.1, U2.4
unnamed: C21.2, U2.5
unnamed: C22.2, U2.2
unnamed: C23.2, U2.6
unnamed: C25.1, JP2.1
unnamed: C26.1, JP4.1
unnamed: C33.2, R69.1, XA1.AREF
unnamed: C38.1, D12.2, F2.1
unnamed: C39.1, C40.1, F3.1, U5.3
unnamed: C43.1, R71.2, R72.1, R73.2
unnamed: C49.2, R77.2, R78.2, U6.4
unnamed: C56.2, JP13.3, R83.2, U7.4
unnamed: D7.2, LED3.1
unnamed: D8.2, LED5.1
unnamed: D9.2, LED7.1
unnamed: D10.2, LED8.1
unnamed: D27.1, JP3.2
unnamed: D27.2, J5.8, R5.2, R6.1
unnamed: D28.1, JP5.2
unnamed: D28.2, J5.7, R7.1, R8.1
unnamed: IC1.2, R28.1
unnamed: IC1.4, R30.1
unnamed: IC1.5, LED2.2, R32.2
unnamed: IC1.7, LED1.2, R26.2
unnamed: IC2.2, R39.1
unnamed: IC2.4, R42.1
unnamed: IC2.5, LED6.2, R45.2
unnamed: IC2.7, LED4.2, R37.2
unnamed: J1.a4, JP1.2
unnamed: JP13.2, R82.2
unnamed: LED1.1, R25.1
unnamed: LED2.1, R31.1
unnamed: LED3.2, R33.2
unnamed: LED4.1, R36.1
unnamed: LED5.2, R40.2
unnamed: LED6.1, R44.1
unnamed: LED7.2, R48.2
unnamed: LED8.2, R52.2
unnamed: LED9.1, Q7.5, Q7.6
unnamed: LED9.2, R53.1
unnamed: LED10.1, R59.1
unnamed: LED10.2, U2.9
unnamed: LED11.1, R23.1
unnamed: LED12.1, R70.1
unnamed: LED13.1, R68.1
unnamed: Q1.2, R50.1
unnamed: Q1.4, R62.1
unnamed: Q2.2, R60.2
unnamed: Q2.4, R61.2
unnamed: Q3.2, R63.1
unnamed: Q3.4, R64.1
unnamed: Q4.2, R65.1
unnamed: Q4.4, R66.2
unnamed: Q5.1, R34.1
unnamed: Q6.1, R43.1
unnamed: Q7.2, R55.2, R67.2
unnamed: Q7.4, R90.1
unnamed: Q8.1, R49.1
unnamed: Q9.1, R54.1
unnamed: R2.2, R86.2
unnamed: R57.2, S1.1, S1.4
unnamed: S1.2, S1.5, XA1.RST
O2: C51.1, J1.a20, R79.1
RX3C: J1.a6, U2.13
RXD3-MCU: U2.12, XA1.D15
SPAREout1: D6.2, J1.b16, Q4.7, Q4.8
STEP-A1: J1.b21, P1.12
STEP-A2: J1.b22, P1.11
STEP-B1: J1.b20, P1.13
STEP-B2: J1.b19, P1.14
STEP-MCU: P1.7, XA1.D17
TACH: J1.a9, Q7.7, Q7.8, R47.1, R90.2
TPS: C47.1, J1.a23, R76.1
TX3C: J1.a7, U2.8, U2.14
TXD3-MCU: U2.11, XA1.D14
VR1-: J1.a11, J5.1
VR2-: J1.a13, J5.4
VVT: D3.2, J1.b15, Q1.5, Q1.6

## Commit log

2022-07-07 Add files via upload
    Added files for V1.2
    [ANALOG.sch, CLAMPS.sch, COMMUNICATIONS.sch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]
2023-04-23 Added PickAndPlace file
    [JLC_K44V12PickAndPlace.xls]
